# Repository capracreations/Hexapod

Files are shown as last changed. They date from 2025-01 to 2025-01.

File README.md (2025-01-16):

# Hexapod
## Overview
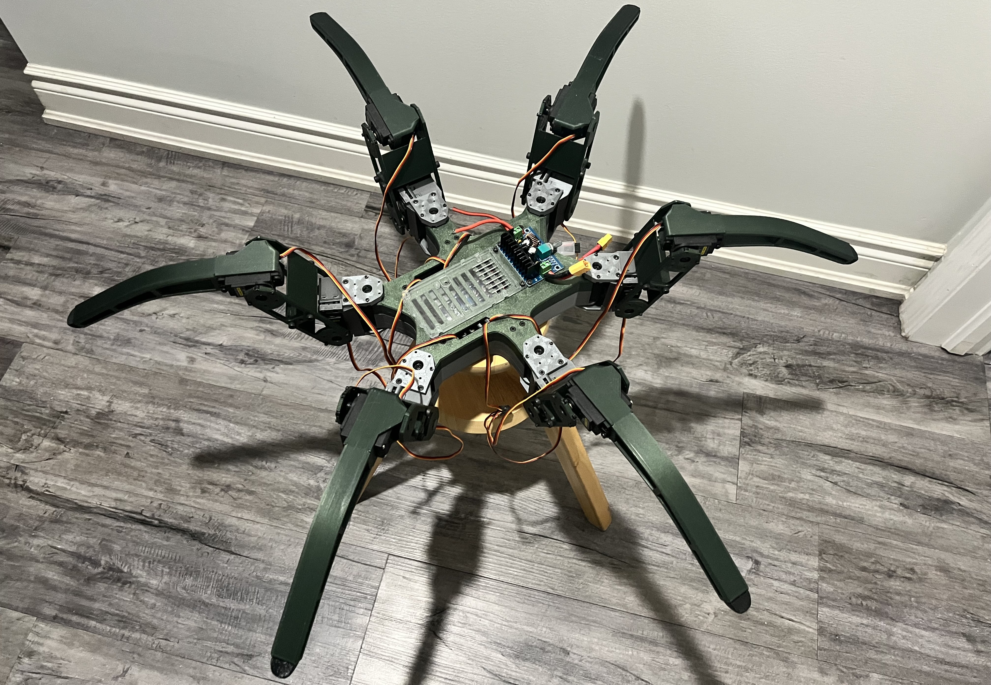
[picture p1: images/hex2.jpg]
  
Six-legged articulated robotic walker which can be controlled with a gamepad through 2.4GHz transceivers. The Hexapod uses 18 MG996R 9-13kg/cm at 5.0V.

## Please Read
The code and files within this repository are currently a **_WORK IN PROGRESS_** and as such I cannot ensure that all the code provided will be in a usable/stable form as I can only work on it during my free time. The design of the Hexapod has not been finalized and is subject to change and modification at any time. Please refer back to this repo from time to time for code and model updates if available. All external resources used (except for product pages) have been referenced within the **_resources_** below, please refer to them for additional info. **_Ryan Mirch's_** hexapod code is used to assist logic and structure within parts of my code; See **_resources_** below for repo.

## Requirements
This project can be a bit lengthy and may test your skills -as it has mine- in design, electronics and code logic, and such it is necessary to be prepared for the task, below is a list of softwares and equipment that will be required to create your own hexapod.
### Softwares
- CAD Software (Solidworks, Fusion360, Onshape)
- 3D-printing Slicer (Cura, Prusaslicer)
- Arduino IDE 2.0 or higher
### Hexapod
- 3D-printer
- 4kg PETG filament, any brand and colour(s)
- Arduino Mega
- 18x MG996R 9-13kg/cm Servos
- NRF24L01 2.4GHz tranceiver module
- Hexapod Arduino PCB Shield (See **_Arduino Ant Hexapod_** in resources for PCB files)
- 12V to 5V Buck DC converter
- 11.1V (3 Cell) Lipo battery
- M.# bolt and nut set
### RF Controller
- Arduino Nano
- NRF24L01 2.4GHz transceiver module
- 2x PCB joystick modules
- 3x PCB push buttons
- 2x PCB slider potentiometer modules
- Switch (2-pins)
- 9V battery

## Inverse Kinematics Solution
Written and worked inverse kinematics solutions for one leg are provided for clarity and understanding. The solution has already been implemented within the code.

## .STL 3D Model Files
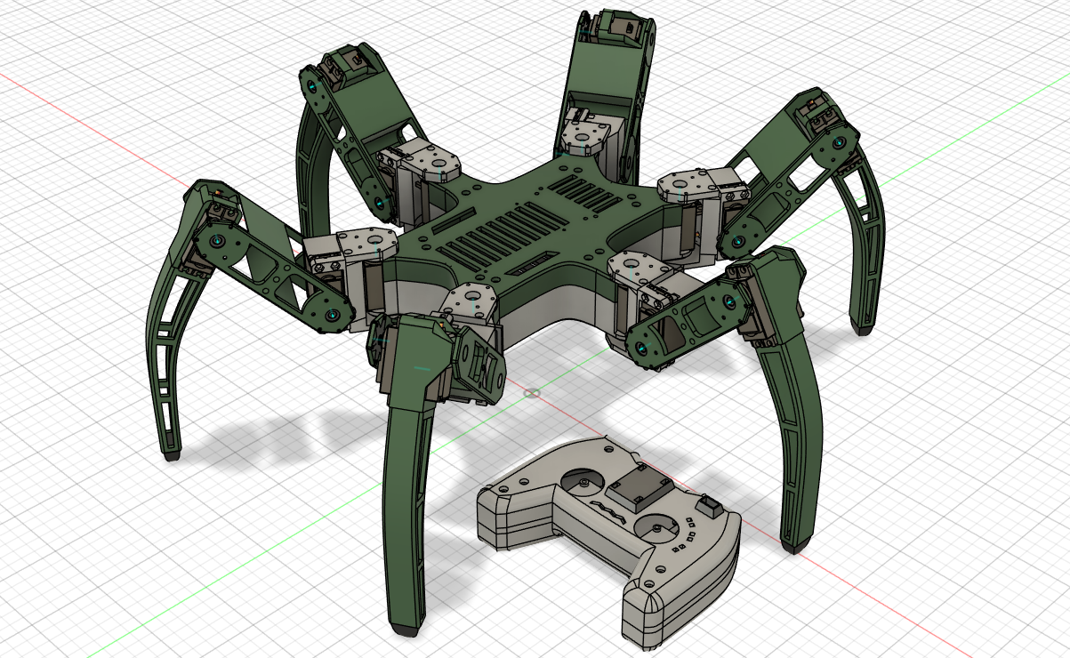
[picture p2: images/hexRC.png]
 
.stl CAD files for the Hexapod and RF Controller are provided for download, parts are designed and toleranced to be **_3D-printed_**. The Hexapod is composed of two main body parts, and six legs with three segments each. Each leg has three rotational joints to allow for a sufficient range of motion.

## Hexapod PCB
For the hexapod to function, a custom Arduino Mega shield is required which can support and drive 18 servo motors at once. How to Mechatronics has already done the hard work for us this time by providing a PCB which can drive up to 24 servos at once, and the files can be downloaded from section 6.1 on their website; see **_Arduino Ant Hexapod_** in the resources below. I also recommend reading through the page to learn more than I can say about assembling the overall circuit. The PCB can be ordered online from PCBWay or JLCPCB (not sponcered by either), if you're worried about messing up while soldering do not worry as they will send you 5 copies.

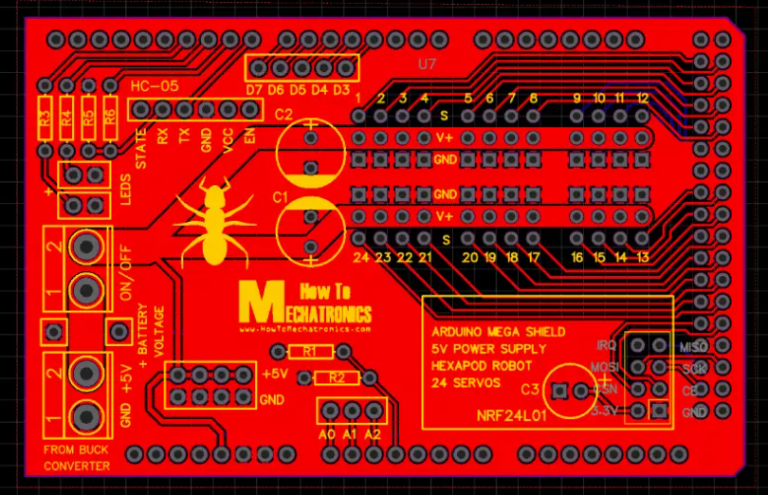
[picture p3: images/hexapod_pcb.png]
How To Mechatronics's servo shield

### Resistors
- R1 = 2KΩ
- R2 = 1KΩ
- R3 = R4 = 220Ω
- R5 = 1KΩ
- R6 = 2KΩ
### Capacitors
- C1 = C2 = 10V/470μF
- C3 = 10V/47μF

## Arduino Code Files
For ease of use and to limit confusion please note that the main code is always assigned the **_.ino_** file type. All **_.h_** and **_.cpp_** type files are **_declarations and definitions_** for objects or functions used within the main **_.ino_** code. To be able to use the code in a "plug and play" style, download the entire root file as a .zip and extract to where desired. From there open the main **_.ino_** file within "Arduino Code/Hexapod" as is and it will ask if you want to create and store the **_.ino_** file in a folder of its own name. Select "yes" and transfer the **_.h_** and **_.cpp_** files into the created directory and they should be applied to the main file automatically.

## Resources
-[Ryan Mirch's Hexapod Repo](https://github.com/Ryan-Mirch/Aecerts_Hexapod_V1/tree/main)  
-[Arduino Ant Hexapod](https://howtomechatronics.com/projects/arduino-ant-hexapod-robot/#h-assembling-the-pcb)

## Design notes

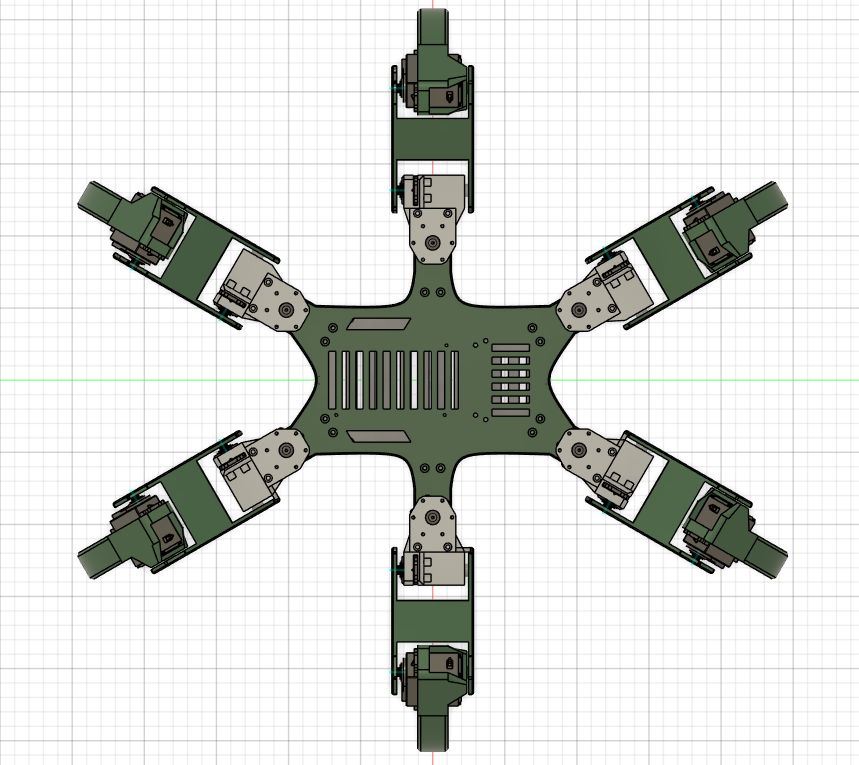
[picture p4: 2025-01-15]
images/hexapod_top.png

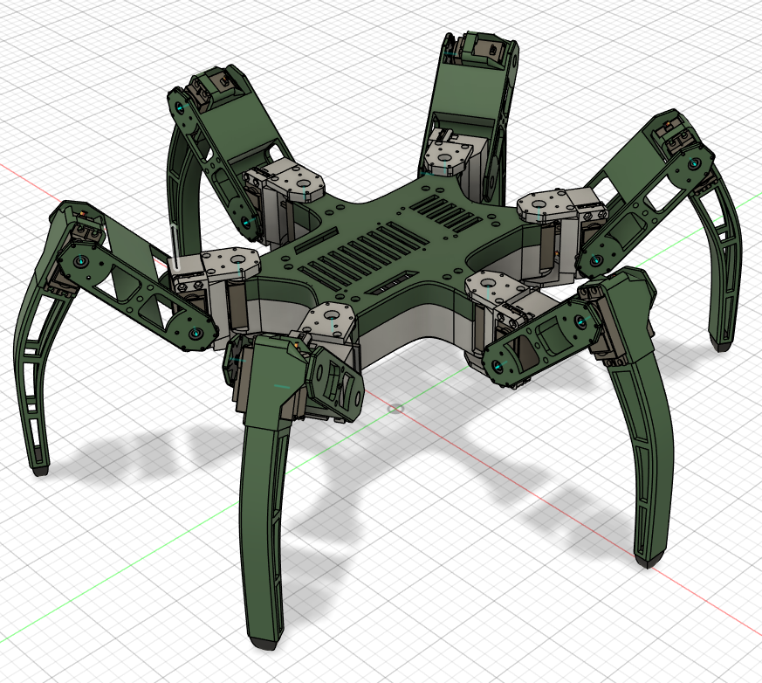
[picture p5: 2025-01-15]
images/hexapod.png

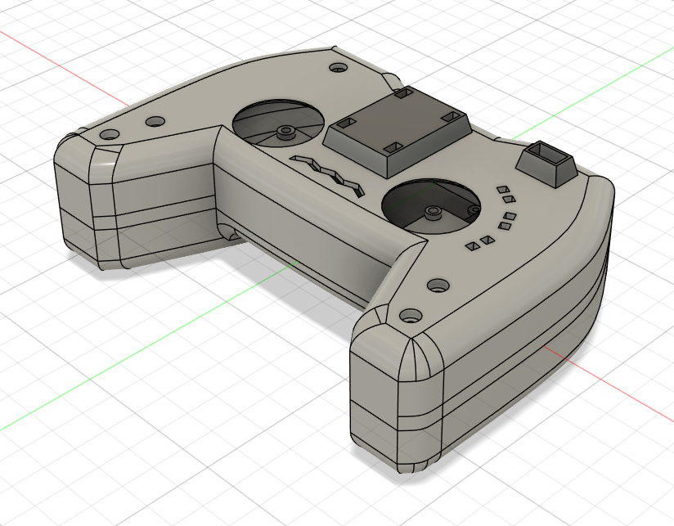
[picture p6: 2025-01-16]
images/RC.png

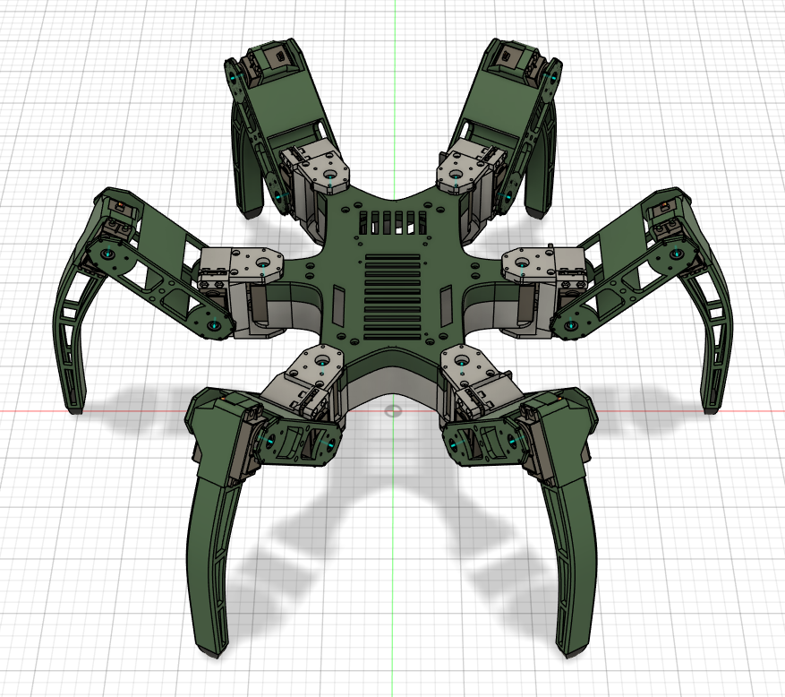
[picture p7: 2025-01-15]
images/hexapod_iso.png

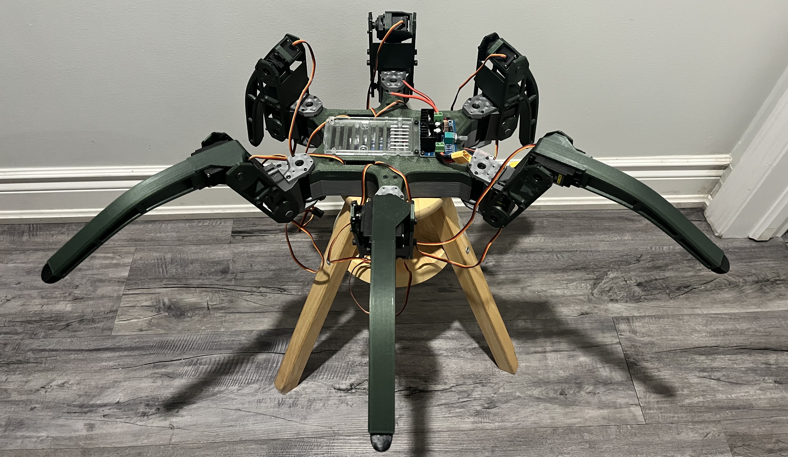
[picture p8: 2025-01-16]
images/hex1.jpg

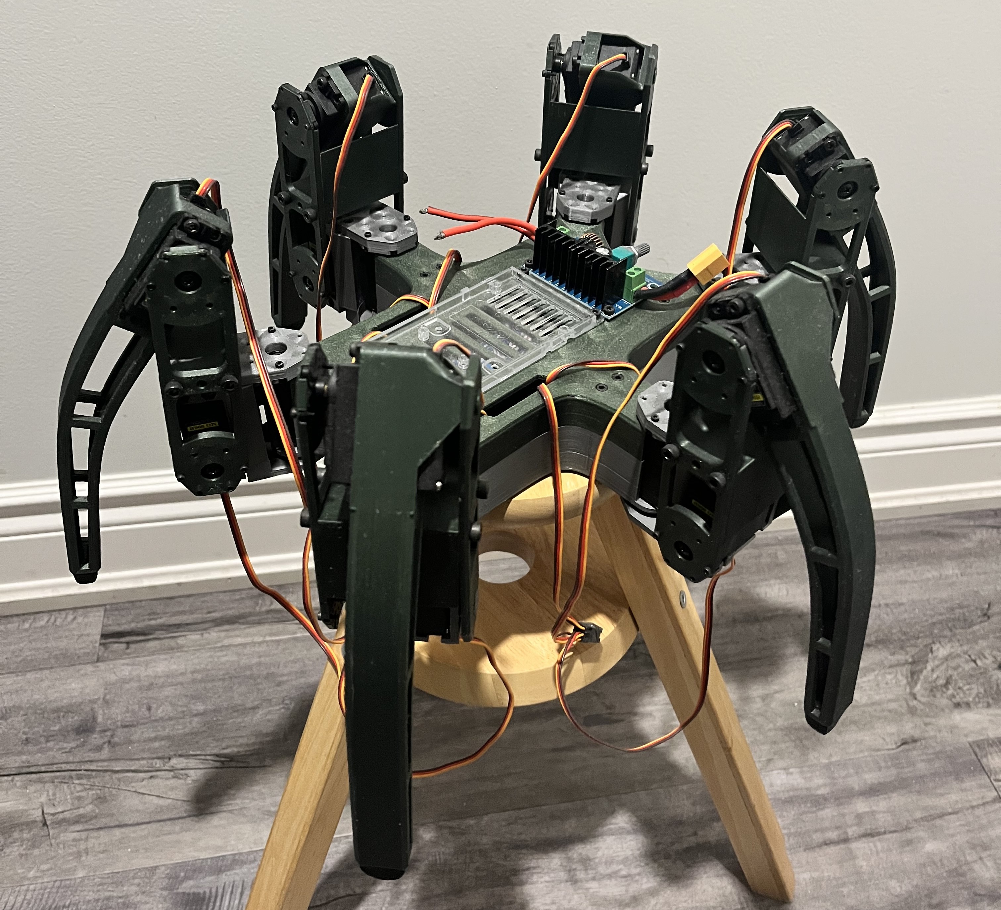
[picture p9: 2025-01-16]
images/hex3.jpg

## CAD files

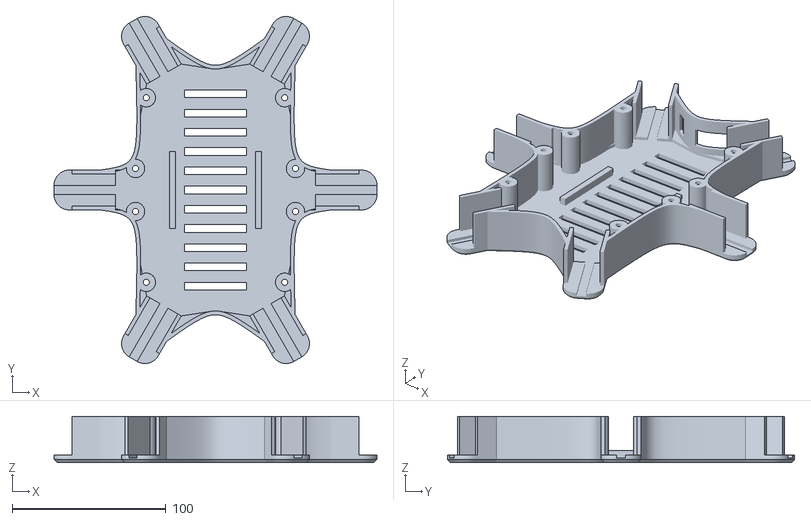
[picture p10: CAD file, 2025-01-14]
Hexapod STL Files/Hexapod Body/Hexabody Bottom.stl
210.0 x 225.7 x 30.0

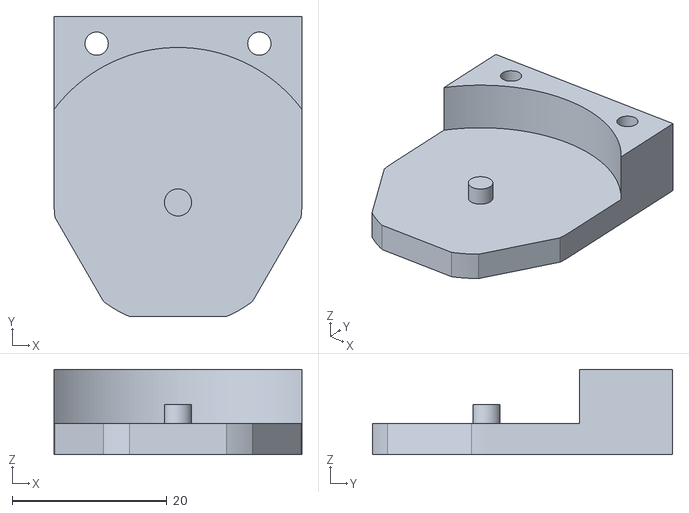
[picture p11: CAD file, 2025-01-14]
Hexapod STL Files/Hexapod Leg/Segment 1/Leg Segment 1-2.stl
32.0 x 38.7 x 11.0

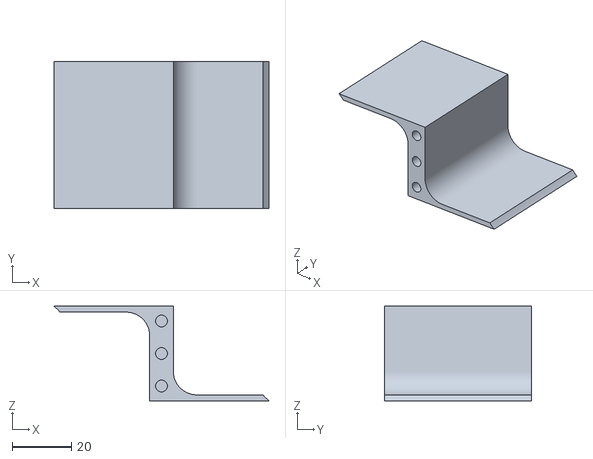
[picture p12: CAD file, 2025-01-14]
Hexapod STL Files/Hexapod Leg/Segment 2/Leg Segment 2-2.stl
72.8 x 49.8 x 32.0

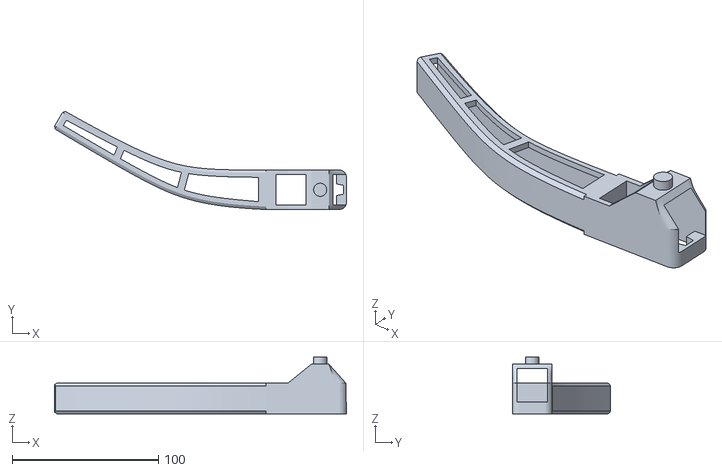
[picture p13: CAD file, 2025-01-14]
Hexapod STL Files/Hexapod Leg/Segment 3/Leg Segment 3.stl
199.8 x 67.1 x 38.8

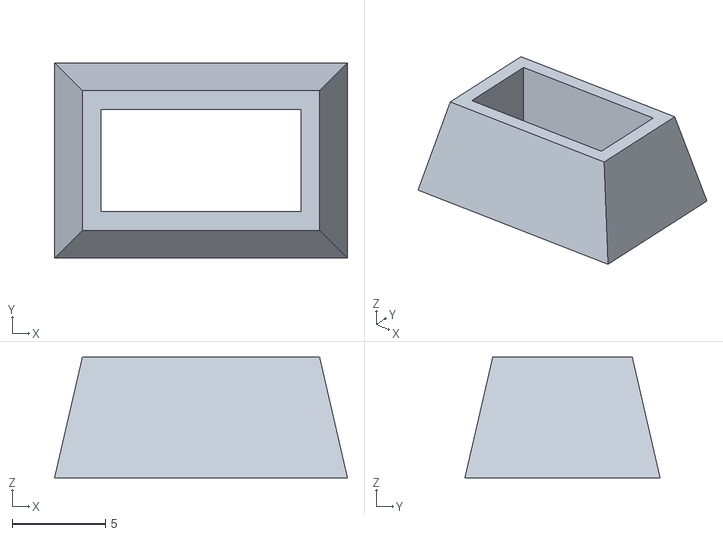
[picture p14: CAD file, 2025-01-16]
Hexapod STL Files/RC Controller/RC NRF Support.stl
15.8 x 10.5 x 6.50

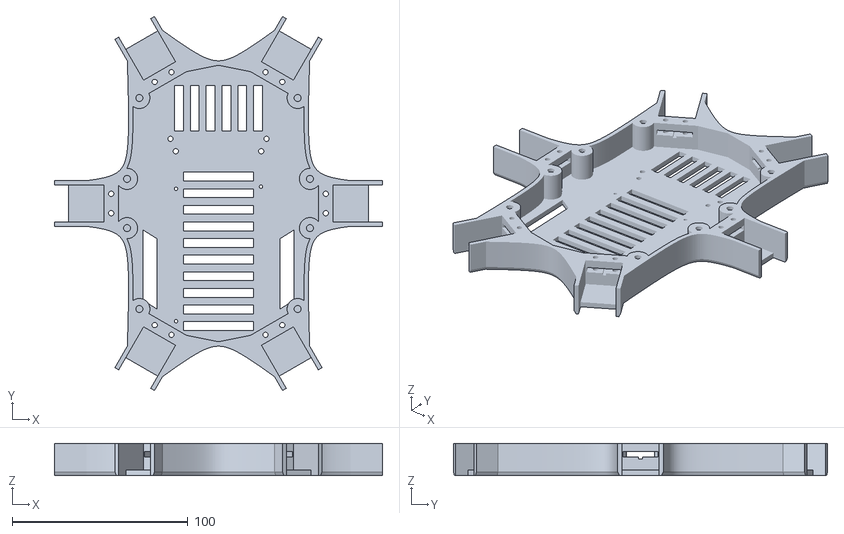
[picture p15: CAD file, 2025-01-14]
Hexapod STL Files/Hexapod Body/Hexabody Top.stl
186.5 x 212.6 x 18.2

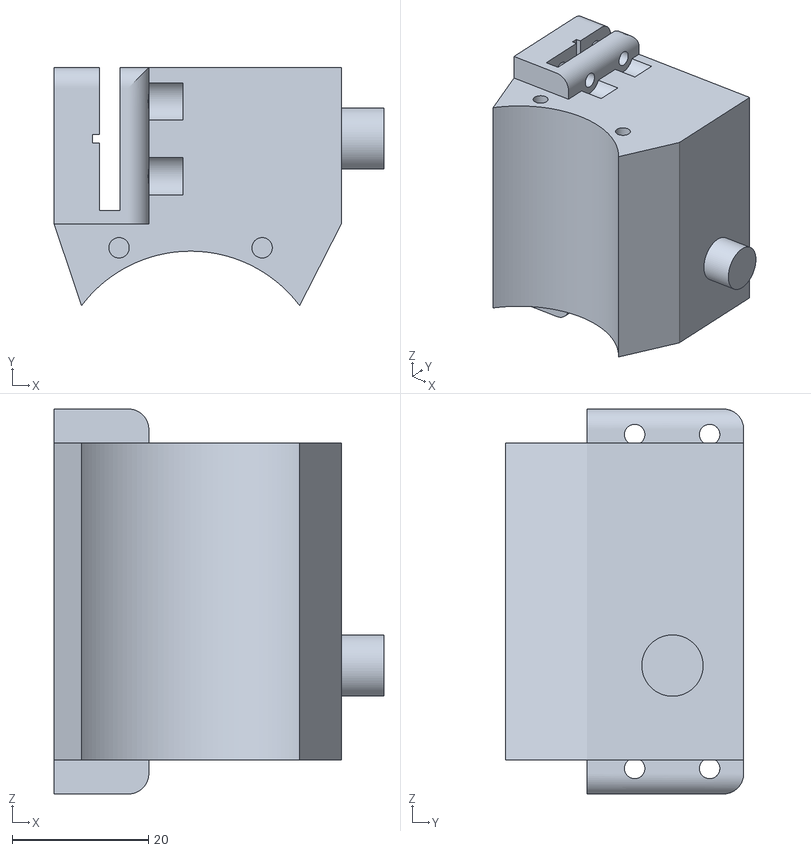
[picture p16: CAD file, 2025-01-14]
Hexapod STL Files/Hexapod Leg/Segment 1/Leg Segment 1-1.stl
48.4 x 35.0 x 56.5

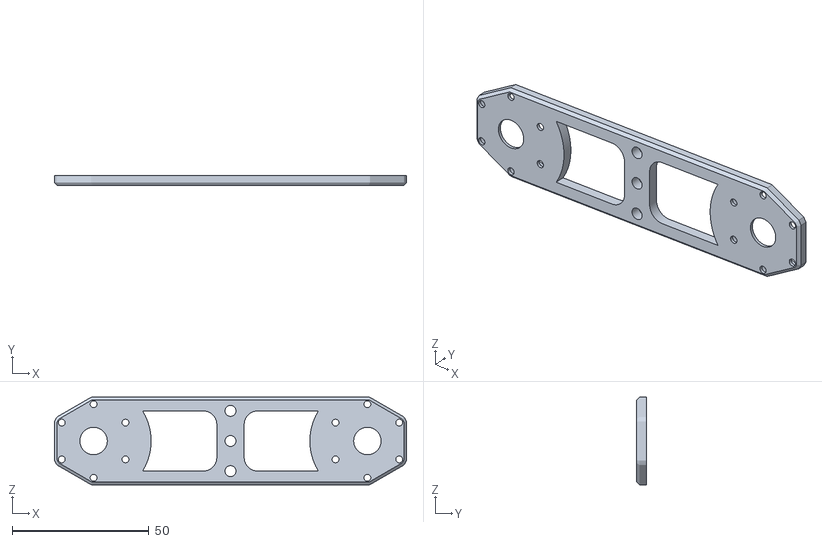
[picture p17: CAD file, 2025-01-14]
Hexapod STL Files/Hexapod Leg/Segment 2/Leg Segment 2-1.stl
128.6 x 3.50 x 32.0

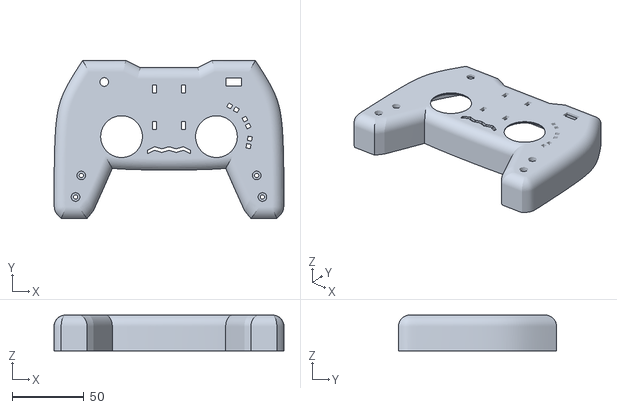
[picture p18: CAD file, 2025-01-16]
Hexapod STL Files/RC Controller/RC Top.stl
160.0 x 110.0 x 25.0

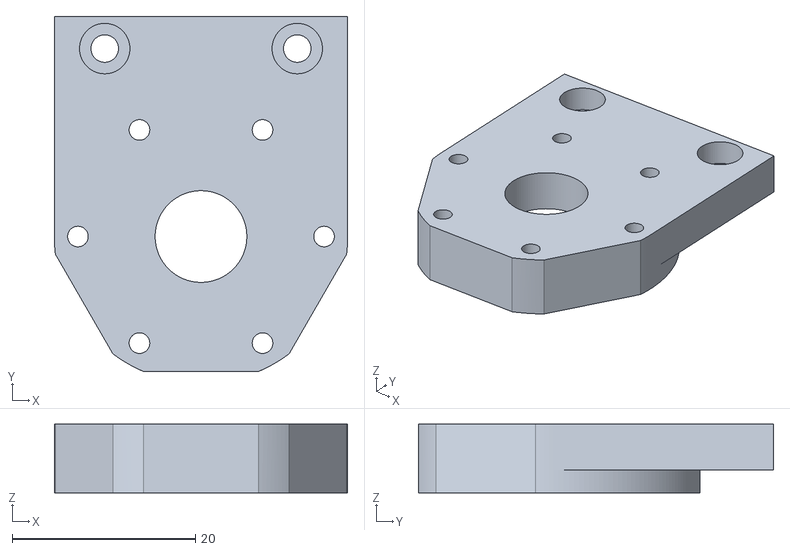
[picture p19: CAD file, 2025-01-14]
Hexapod STL Files/Hexapod Leg/Segment 1/Leg Segment 1-3.stl
32.0 x 38.7 x 7.50

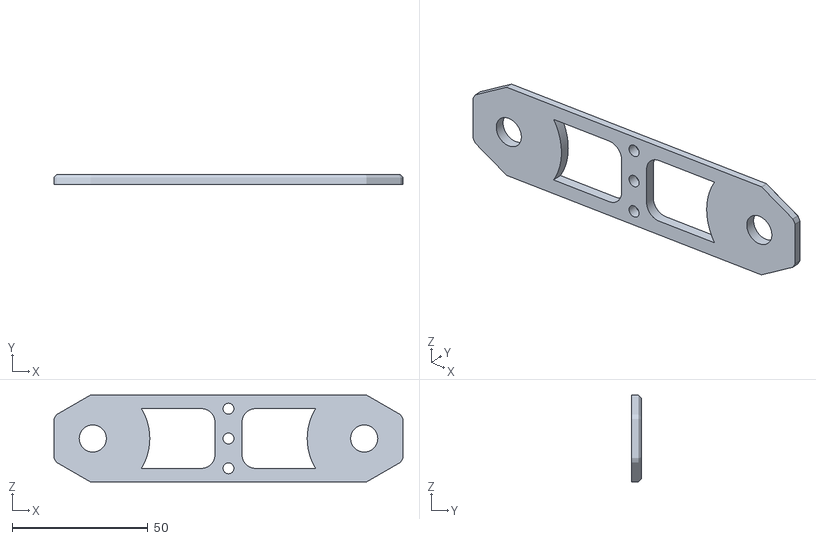
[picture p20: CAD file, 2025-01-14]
Hexapod STL Files/Hexapod Leg/Segment 2/Leg Segment 2-3.stl
128.6 x 3.50 x 32.0

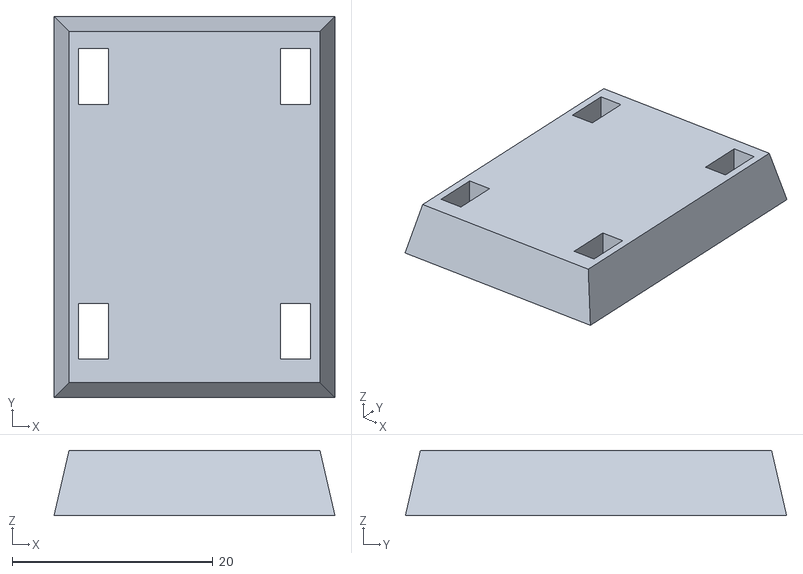
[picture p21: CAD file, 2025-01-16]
Hexapod STL Files/RC Controller/RC Slider Riser.stl
28.0 x 38.0 x 6.50

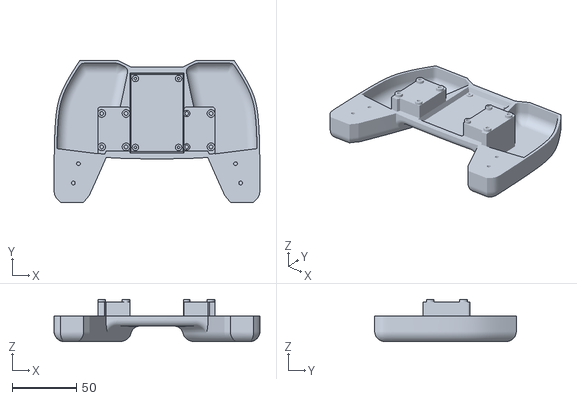
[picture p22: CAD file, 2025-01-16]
Hexapod STL Files/RC Controller/RC Bottom.stl
160.0 x 110.0 x 32.8

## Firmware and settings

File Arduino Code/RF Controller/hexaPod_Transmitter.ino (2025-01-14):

#include "Transmitter.h"


void setup() {

  Serial.begin(9600);
  radioSetup();
  pinModeSetup();
}

void loop() {

  if(!Radio.begin() && !Radio.isChipConnected()) {

    Serial.println("Radio Not Responding :/");
    while(1) {}
  }
  else {

    timeLastInput = millis();
    bool connected = outputRead();

    if(connected) {
  
      outputSend();
    }

    //delay();
  }
}

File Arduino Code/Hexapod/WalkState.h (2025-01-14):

#ifndef WALKSTATE_H
#define WALKSTATE_H
#include "Initialization.h"
#include "Receiver.h"
#include "Vectors.h"
#include "HexMode.h"
#include "Bezier.h"
#include "Hex.h"


float forwardAmount;
float turnAmount;
float velocityMult;
float strideLengthMult;
float liftHeightMult;
float pushFraction;
float maxStrideLength;
float maxVelocity;
float globalVelMult;
float globalRotMult;

float strideMult[6] = {1, 1, 1, -1, -1, -1};  //possible physical error
float rotMult[6] = {-1, 0, 1, 1, 0, -1};      //possible physical error

float disCenterToLeg[6] = {267.33, 250.177, 267.33, 267.33, 250.177, 267.33};
float defaultHeight = -71; // Height value based on distance to ground from lowest point of hexapod body
float height[2]; //Current and previous Height Values

float legAngle = 60;
float liftHeight = 125;       //possible physical error 
float landHeight = 30;        //possible physical error
float strideOvershoot = 10;   //possible physical error

int amountCtrlPnts;
int amountRotCtrlPnts;
Vector3D ctrlPnts[4];
Vector3D rotCtrlPnts[5];

Vector2D joy1Target = Vector2D(0,0);
float joy1TarMag = 0;
Vector2D joy1Current = Vector2D(0,0);
float joy1CurMag = 0;
Vector2D joy2Target = Vector2D(0,0);
float joy2TarMag = 0;
Vector2D joy2Current = Vector2D(0,0);
float joy2CurMag = 0;

LegState stateLeg[6];
GaitCycle appliedCycle;

float points = 1000;
int cycleProg[12];
float tArr[6];

                 // Leg 1       | Leg 2       | Leg 3
          // Slot = 10, 11, 12  |  6,  7,  8  |  2,  3,  4 
int pins[6][3] = { {31, 32, 33}, {27, 28, 29}, {23, 24, 25},
                   {44, 43, 42}, {40, 39, 38}, {36, 35, 34} };
          // Slot = 23, 22, 21  | 19, 18, 17  | 15, 14, 13
                 // Leg 4       | Leg 5       | Leg 6  

Hexapod Hex(pins);


void attachHex() {

  attach(Hex);
}


void mapInputs() {

  float Joy1Y = map(Controller.J1_Y, 0, 1023, -200, 200);
  float Joy1X = map(Controller.J1_X, 0, 1023, -200, 200);
  float Joy2X = map(Controller.J2_X, 0, 1023, -200, 200);
  float Joy2Y = map(Controller.J2_Y, 0, 1023, -200, 200);

  joy1Target = Vector2D(Joy1X, Joy1Y);
  joy1TarMag = constrain(calcHypotenuse(abs(Joy1X), abs(Joy1Y)), 0, 100);
  joy2Target = Vector2D(Joy2X, Joy2Y);
  joy2TarMag = constrain(calcHypotenuse(abs(Joy2X), abs(Joy2Y)), 0, 100);

  joy1Current = lerp(joy1Current, joy1Target, 0.08);
  joy1CurMag = lerp(joy1CurMag, joy1TarMag, 0.08);
  joy2Current = lerp(joy2Current, joy2Target, 0.12);
  joy2CurMag = lerp(joy2CurMag, joy2TarMag, 0.12);  

  Controller.S1 = map(Controller.S1, 0, 1023, 0, 100);
  Controller.S2 = map(Controller.S2, 0, 1023, 0, 100);

  height[1] = height[0];
  height[0] = Controller.S2 * -1 + defaultHeight  ;

  globalVelMult = map(Controller.S1, 0, 100, 10, 100) * 0.01;
  globalRotMult = map(Controller.S1, 0, 100, 40, 130) * 0.01;
}


Vector3D getGaitPoint(int id, float pushFraction) {

  float rotStrideLength = turnAmount * globalRotMult;
  joy1Current = joy1Current * Vector2D(1, strideLengthMult); 
  joy1Current.x = constrain(joy1Current.x, -maxStrideLength/2, maxStrideLength/2) * globalVelMult;
  joy1Current.y = constrain(joy1Current.y, -maxStrideLength/2, maxStrideLength/2) * globalVelMult;

  float weightSum = abs(forwardAmount) + abs(turnAmount);

  if(tArr[id] < pushFraction) {

    if(stateLeg[id] != Pushing) {

      Hex.L[id].setStartPnts(id);
      stateLeg[id] = Pushing;
    }

    amountCtrlPnts = 2;
    ctrlPnts[0] = Hex.L[id].walkStartPnts[id];
    ctrlPnts[1] = Vector3D(joy1Current.x * strideMult[id] + disCenterToLeg[id], -joy1Current.y * strideMult[id], height[0]).rotate(legAngle * rotMult[id], Vector2D(disCenterToLeg[id], 0));
    Vector3D vectorPoint = GetPointOnBezierCurve(ctrlPnts, amountCtrlPnts, mapFloat(tArr[id], 0, pushFraction, 0 ,1));

      //vectorPoint.print();

    amountRotCtrlPnts = 3;
    rotCtrlPnts[0] = Hex.L[id].walkStartPnts[id];
    rotCtrlPnts[1] = {disCenterToLeg[id] + 40, 0, height[0]};
    rotCtrlPnts[1] = {disCenterToLeg[id], rotStrideLength, height[0]};
    Vector3D angularPoint = GetPointOnBezierCurve(rotCtrlPnts, amountRotCtrlPnts, mapFloat(tArr[id], 0, pushFraction, 0 ,1));

      //angularPoint.print();

    Vector3D transformPoint;
    transformPoint.x = (vectorPoint.x * abs(forwardAmount) + angularPoint.x * abs(turnAmount)) / weightSum;
    transformPoint.y = (vectorPoint.y * abs(forwardAmount) + angularPoint.y * abs(turnAmount)) / weightSum;
    transformPoint.z = (vectorPoint.z * abs(forwardAmount) + angularPoint.z * abs(turnAmount)) / weightSum;

      //transformPoint.print();

    return transformPoint;

  }
  else { 

      Serial.print("1");

    if(stateLeg[id] != Lifting) {

      Hex.L[id].setStartPnts(id);
      stateLeg[id] = Lifting;
    }

    amountCtrlPnts = 4;
    ctrlPnts[0] = Hex.L[id].walkStartPnts[id];
    ctrlPnts[1] = Hex.L[id].walkStartPnts[id] + Vector3D(0, 0, liftHeight * liftHeightMult);
    ctrlPnts[2] = Vector3D(-joy1Current.x + strideMult[id] + disCenterToLeg[id], (joy1Current.y + strideOvershoot) * strideMult[id], height[0] + landHeight).rotate(legAngle * rotMult[id], Vector2D(disCenterToLeg[id], 0));
    ctrlPnts[3] = Vector3D(-joy1Current.x + strideMult[id] + disCenterToLeg[id], joy1Current.y * strideMult[id], height[0]).rotate(legAngle * rotMult[id], Vector2D(disCenterToLeg[id], 0));
    Vector3D vectorPoint = GetPointOnBezierCurve(ctrlPnts, amountCtrlPnts, mapFloat(tArr[id], pushFraction, 1, 0 ,1));

      //vectorPoint.print();

    amountRotCtrlPnts = 5;
    rotCtrlPnts[0] = Hex.L[id].walkStartPnts[id];
    rotCtrlPnts[1] = Hex.L[id].walkStartPnts[id] + Vector3D(0, 0, liftHeight * liftHeightMult);
    rotCtrlPnts[2] = {disCenterToLeg[id] + 40, 0, height[0] + liftHeight * liftHeightMult};
    rotCtrlPnts[3] = {disCenterToLeg[id], -(rotStrideLength + strideOvershoot), height[0] + landHeight};
    rotCtrlPnts[4] = {disCenterToLeg[id], -rotStrideLength, height[0]};
    Vector3D angularPoint = GetPointOnBezierCurve(rotCtrlPnts, amountRotCtrlPnts, mapFloat(tArr[id], pushFraction, 1, 0 ,1));

      //angularPoint.print();

    Vector3D liftPoint;
    liftPoint.x = (vectorPoint.x * abs(forwardAmount) + angularPoint.x * abs(turnAmount)) / weightSum;
    liftPoint.y = (vectorPoint.y * abs(forwardAmount) + angularPoint.y * abs(turnAmount)) / weightSum;
    liftPoint.z = (vectorPoint.z * abs(forwardAmount) + angularPoint.z * abs(turnAmount)) / weightSum;

    //if(liftPoint.z)

      //liftPoint.print();

    return liftPoint;
  }
}
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

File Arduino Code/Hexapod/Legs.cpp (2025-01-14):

#include "Legs.h"


Legs::Legs() {

}


void Legs::attach() {

  Joints[0].attach(coxa, 500, 2500);
  Joints[1].attach(femur, 500, 2500);
  Joints[2].attach(tibia, 500, 2500);
}


void Legs::print() {

  Serial.print("Identifier: ");
  Serial.print(identifier);
  Serial.print("\tS1: ");
  Serial.print(Joints[0].attached());
  Serial.print("\tS2: ");
  Serial.print(Joints[1].attached());
  Serial.print("\tS3: ");
  Serial.print(Joints[2].attached());
  Serial.print("\ncoxa: ");
  Serial.print(coxa);
  Serial.print("\tfemur: ");
  Serial.print(femur);
  Serial.print("\ttibia: ");
  Serial.print(tibia);
  Serial.print("\n\n");
}


void Legs::moveLeg(Vector3D Coords, int id) {

  currentPnts[id] = Coords;

  float X = Coords.x;
  float Y = Coords.y;
  float Z = Coords.z;

  X += oX;
  Y += oY;
  Z += oZ;

  float P = sqrt((Y * Y) + (X * X));
  float Q = P - L1;
  float L0 = sqrt((Q * Q) + (Z * Z));
  float J1 = atan(Y / X) * (180 / PI);
  float A = atan(Z / Q) * (180 / PI);
  float B = acos(((L0 * L0) + (L2 * L2) - (L3 * L3)) / (2 * L0 * L2)) * (180 / PI);
  float J2 = (B + A);
  float J3 = acos(((L2 * L2) + (L3 * L3) - (L0 * L0)) / (2 * L2 * L3)) * (180 / PI);

  //Serial.print(X);
  //Serial.print("\t");
  //Serial.print(Y);
  //Serial.print("\t");
  //Serial.print(Z);
  //Serial.print("\n")

  if(id >= 0 && id < 3) {
  
    Legs::newPosLeft(J1, J2, J3);
  }
  else if(id >= 3 && id < 6) {
  
    Legs::newPosRight(J1, J2, J3);
  }
}


void Legs::moveLeg(Vector3D Coords, Vector3D Base, int id) {

  currentPnts[id] = Coords;

  float X = Coords.x;
  float Y = Coords.y;
  float Z = Coords.z;

  float hX = Base.x;
  float hY = Base.y;
  float hZ = Base.z;

  hX = hX / 0.5;
  X += (oX + hX);
  Y += (oY + hY);
  Z += (oZ - hZ);

  float P = sqrt((Y * Y) + (X * X));
  float Q = P - L1;
  float L0 = sqrt((Q * Q) + (Z * Z));
  float J1 = atan(Y / X) * (180 / PI);
  float A = atan(Z / Q) * (180 / PI);
  float B = acos(((L0 * L0) + (L2 * L2) - (L3 * L3)) / (2 * L0 * L2)) * (180 / PI);
  float J2 = (B + A);
  float J3 = acos(((L2 * L2) + (L3 * L3) - (L0 * L0)) / (2 * L2 * L3)) * (180 / PI);

  if(id >= 0 && id < 3) {
  
    Legs::newPosLeft(J1, J2, J3);
  }
  else if(id >= 3 && id < 6) {
  
    Legs::newPosRight(J1, J2, J3);
  }
}


void Legs::newPosLeft(float J1, float J2, float J3) {

  Joints[0].write(90 + J1);
  Joints[1].write(90 + J2);
  Joints[2].write(180 - J3 - J3_Off);
}


void Legs::newPosRight(float J1, float J2, float J3) {

  Joints[0].write(90 - J1);
  Joints[1].write(90 - J2);
  Joints[2].write(J3 + J3_Off);
}


Vector3D Legs::setStartPnts(int id) {
  
  walkStartPnts[id] = currentPnts[id];   

  return walkStartPnts[id];
}


void Legs::setStartPnts() {
  
  for(int i = 0; i < 6; i++){
    walkStartPnts[i] = currentPnts[i]; 
  }     
}

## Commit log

2025-01-14 Uploaded .STL and .INO files
    Files for Hexapod code and 3D-models commited.
    [Hexabody Bottom.stl, Hexabody Top.stl, Leg Segment 1-1.stl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]
2025-01-16 RC .STLs and image
    [RC Bottom.stl, RC NRF Support.stl, RC Slider Riser.stl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]
